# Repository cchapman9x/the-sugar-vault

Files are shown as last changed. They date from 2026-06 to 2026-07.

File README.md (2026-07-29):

# The Sugar Vault

<p align="center">
  Final build front view
  Final build front view
  Final build side view
</p>

<hr>

**Project Status:** Completed ✅

<hr>

## Project Overview

The Sugar Vault is an Arduino-controlled candy dispenser that uses an Arduino Nano, NEMA 17 stepper motor, A4988 stepper motor driver, push button, LED indicator, DC-DC buck converter, and 3D-printed mechanical parts to dispense candy.

The goal of this project was to design and build a functional candy dispensing machine that uses a motorized dispensing system instead of a traditional hand-turned mechanical mechanism. The final system is activated when the user presses the green button on the front of the machine. When pressed, the button sends a signal to the Arduino Nano, which then controls the A4988 stepper motor driver. The motor driver powers the NEMA 17 stepper motor, causing the dispensing wheel to rotate. During the dispensing cycle, the green LED turns on to indicate that the wheel is moving. One button press rotates the dispensing wheel 360° to release candy.

This project was built to refresh and strengthen my basic engineering skills while giving me a better understanding of how to format, document, and organize future electronics and mechanical design projects.

<hr>

## Main Components

<table>
  <tr>
    <th>Component</th>
    <th>Image</th>
  </tr>

  <tr>
    <td>Arduino Nano</td>
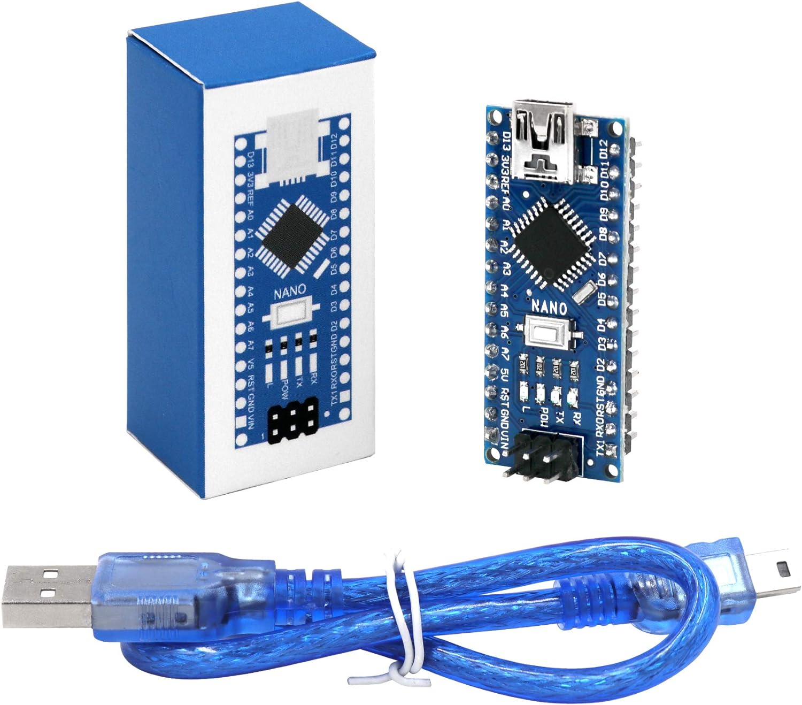
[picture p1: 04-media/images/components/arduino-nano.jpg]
Arduino Nano
    <td></td>
  </tr>

  <tr>
    <td>A4988 stepper motor driver</td>
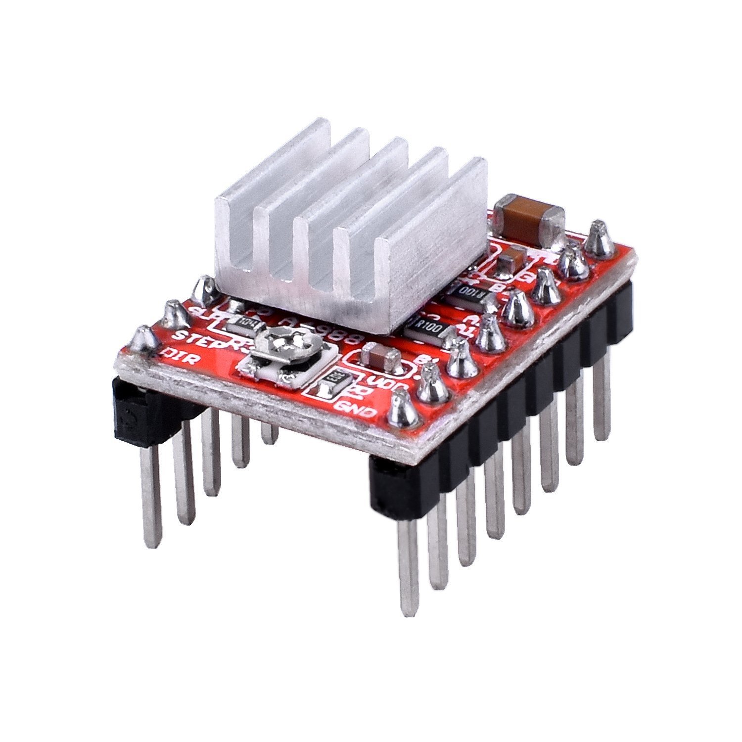
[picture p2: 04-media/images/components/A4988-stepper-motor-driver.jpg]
A4988 stepper motor driver
    <td></td>
  </tr>

  <tr>
    <td>NEMA 17 stepper motor</td>
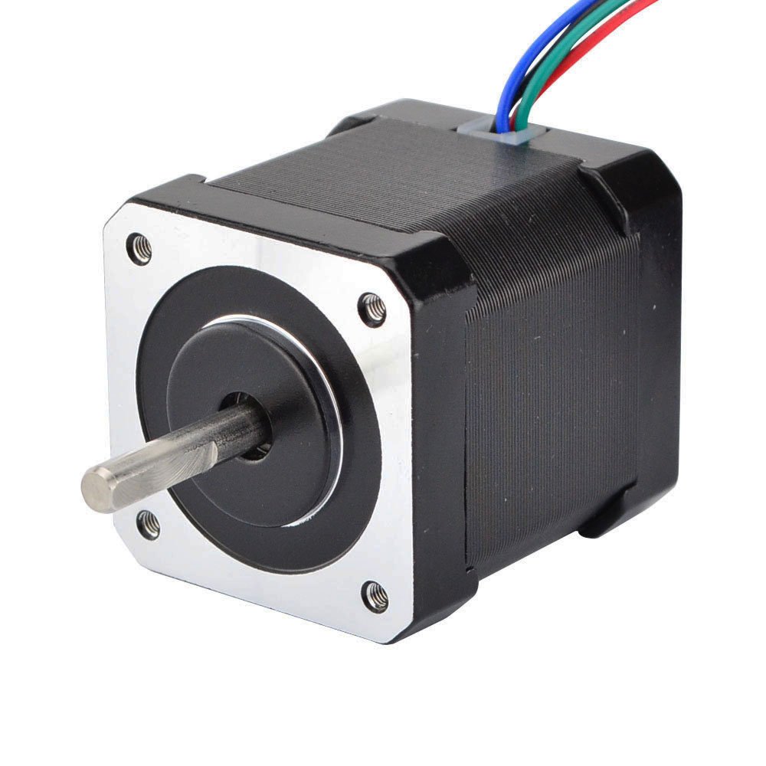
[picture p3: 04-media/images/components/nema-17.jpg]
NEMA 17 stepper motor
    <td></td>
  </tr>

  <tr>
    <td>12V 2A power supply</td>
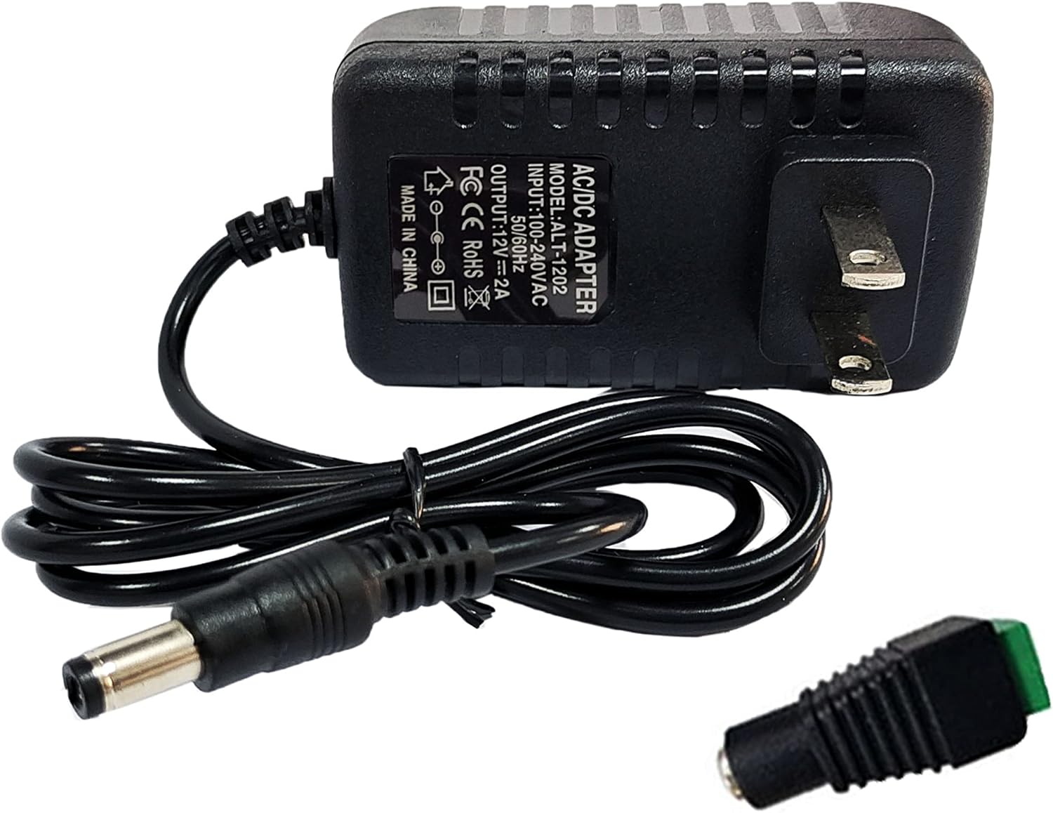
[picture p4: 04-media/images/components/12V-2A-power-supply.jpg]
12V 2A power supply
    <td></td>
  </tr>

  <tr>
    <td>DC-DC buck converter</td>
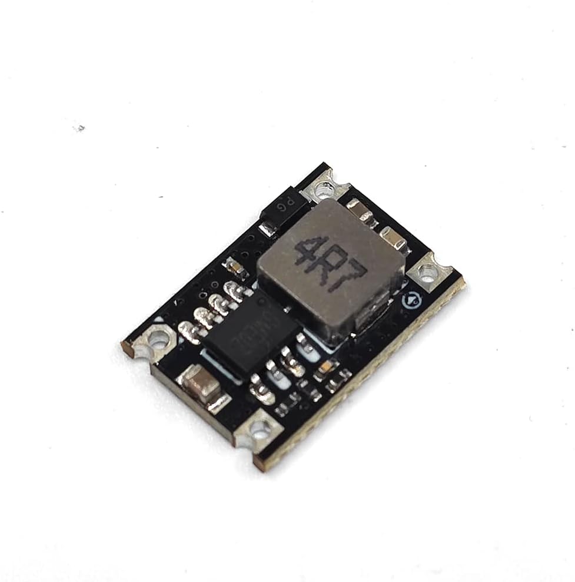
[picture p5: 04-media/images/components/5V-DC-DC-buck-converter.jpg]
DC-DC buck converter
    <td></td>
  </tr>

  <tr>
    <td>Push button</td>
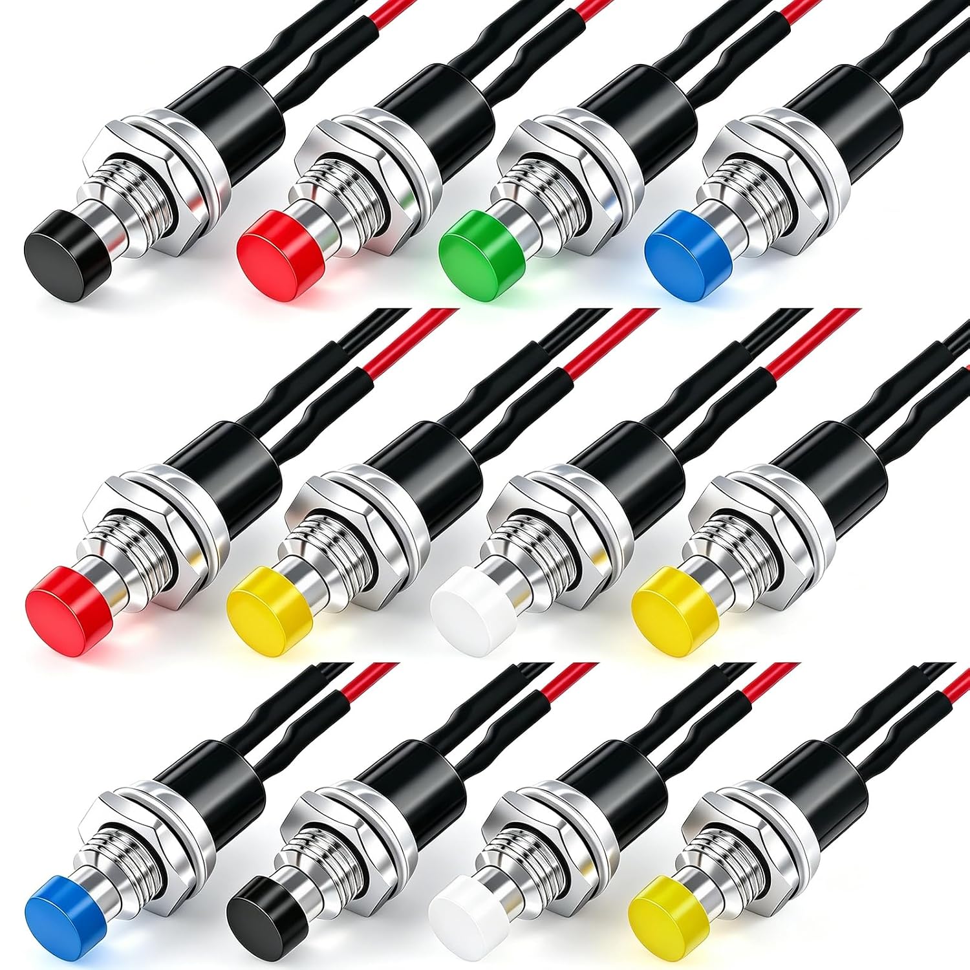
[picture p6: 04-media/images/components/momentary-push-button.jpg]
Push button
    <td></td>
  </tr>

  <tr>
    <td>Green LED</td>
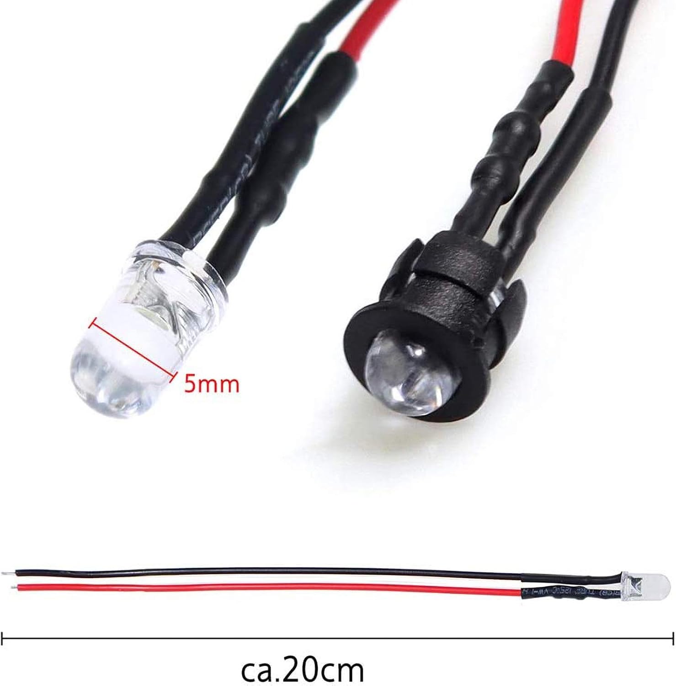
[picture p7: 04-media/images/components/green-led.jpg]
Green LED
    <td></td>
  </tr>

  <tr>
    <td>2.2 kΩ resistor</td>
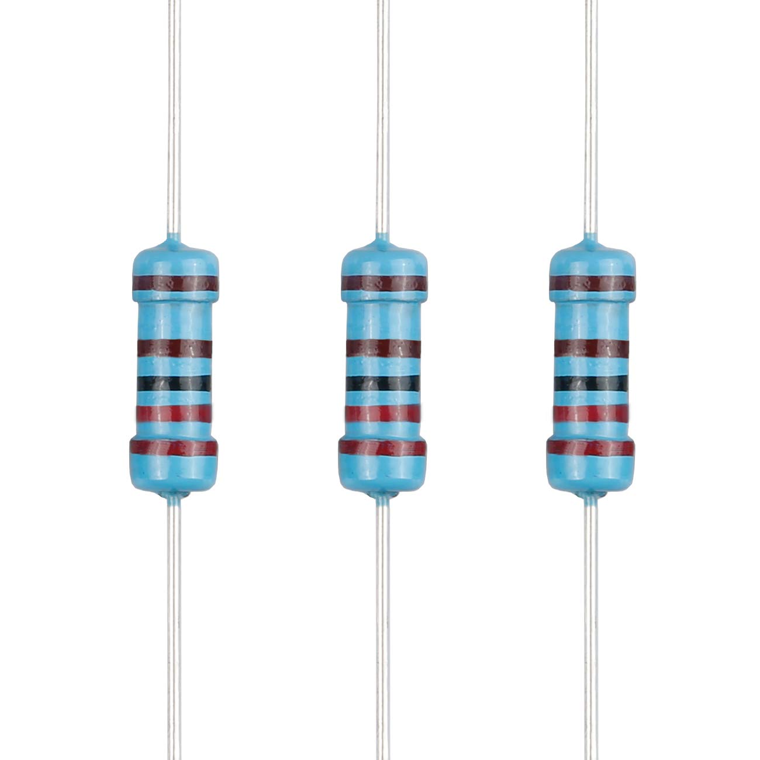
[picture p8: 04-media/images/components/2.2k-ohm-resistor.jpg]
2.2 kΩ resistor
    <td></td>
  </tr>

  <tr>
    <td>220 µF 25V electrolytic capacitor</td>
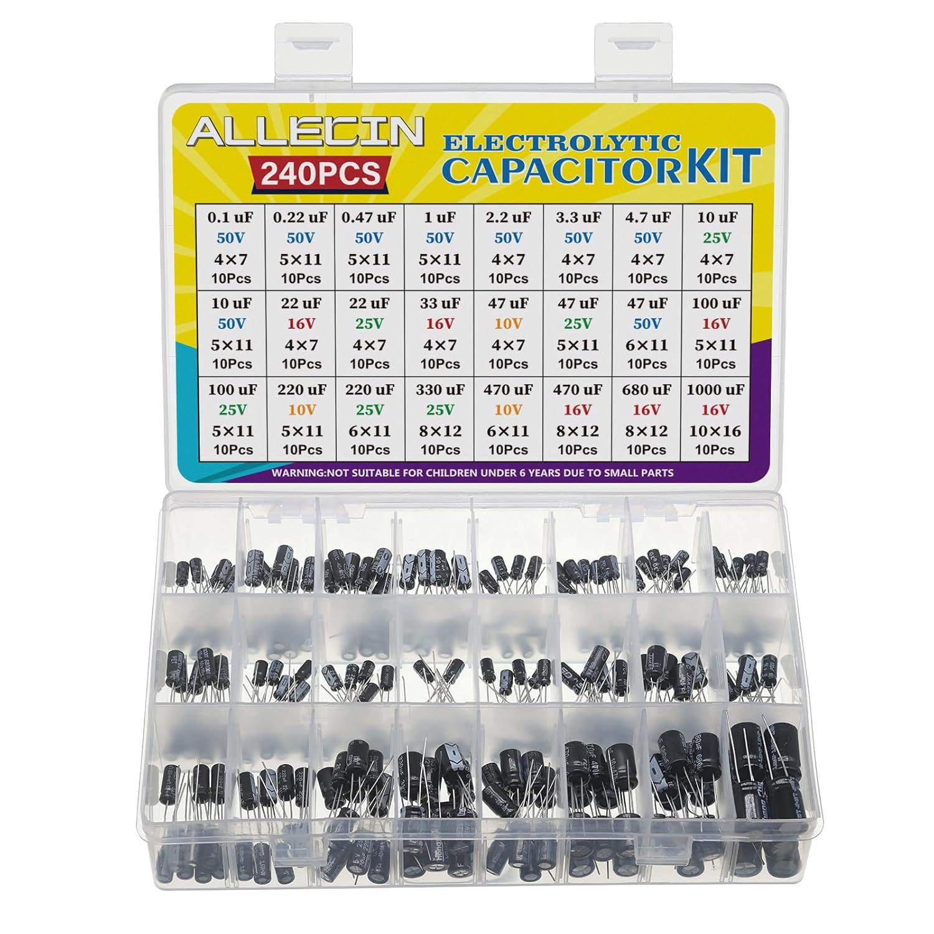
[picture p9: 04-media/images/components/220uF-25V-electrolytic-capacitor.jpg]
220 µF 25V electrolytic capacitor
    <td></td>
  </tr>

  <tr>
    <td>Red & White PETG</td>
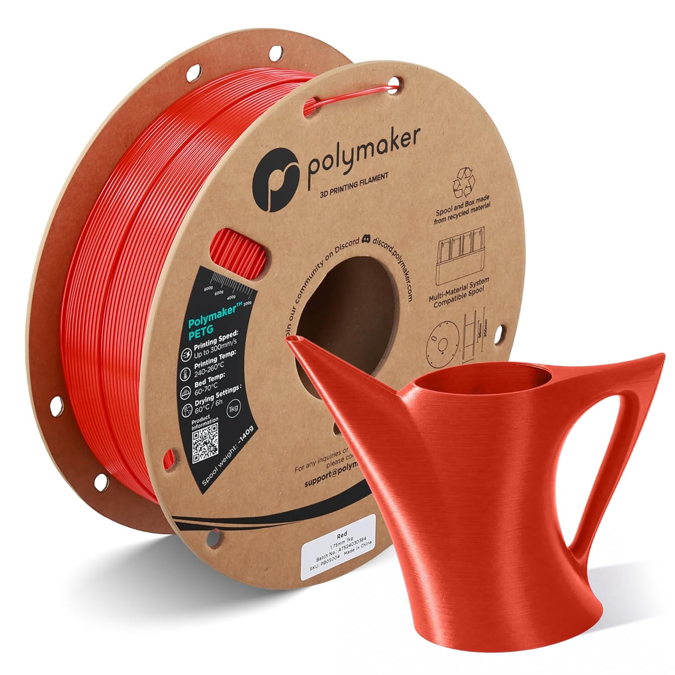
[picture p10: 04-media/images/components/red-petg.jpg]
    <td></td>
  </tr>

  <tr>
    <td>12" Clear Acrylic Tube</td>
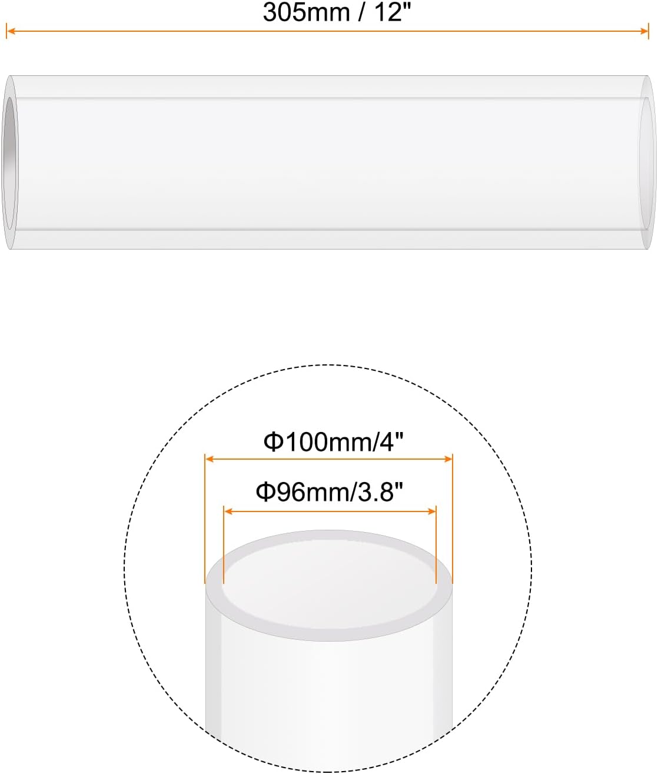
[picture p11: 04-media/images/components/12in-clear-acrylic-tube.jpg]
    <td></td>
  </tr>
</table>

<hr>

## Full Project Documentation

📄 [Open the complete Sugar Vault technical report](01-docs/the-sugar-vault-main.pdf)

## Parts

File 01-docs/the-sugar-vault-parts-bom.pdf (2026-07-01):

# The Sugar Vault

An Arduino controlled candy & chocolate dispensing machine

PARTS+BOM

Start Date: 5/18/2026
End Date: 6/28/2026
Software Used: Google Docs, SOLIDWORKS, draw.io, Arduino IDE, GitHub, Bambu Studio Project GitHub: https://github.com/cchapman9x/the-sugar-vault

Project Creator:
- Caleb Chapman | Montgomery College | Electrical Engineering

Parts Required

Part | Qty | Purpose
Arduino Nano | x1 | Main microcontroller used to control the dispenser
A4988 Stepper Motor Driver | x1 | Controls the NEMA 17 stepper motor
NEMA 17 Stepper Motor | x1 | Rotates the dispensing wheel
12V 2A Power Supply | x1 | Main external power source for the system
DC-DC Buck Converter | x1 | Steps the 12V supply down to a safe voltage for the Arduino
Momentary Push Button | x1 | User input used to start the dispensing cycle
Green LED | x1 | Visual indicator that turns on while dispensing
2.2kΩ Resistor | x1 | Limits current for the LED
220μF 25V Electrolytic Capacitor | x1 | Helps smooth power near the stepper motor driver
Red & White Filament | As Needed | Used to create the 3D printed parts
12” Clear Acrylic Tube ⌀100mm / 4” | x1 | Used to store the candy and acts as the hopper of the system

1

Jumper Wires / Hookup Wires | As Needed | Used to connect the circuit components
Screw Terminals / Connectors | As Needed | Used for power and wiring connections
Breadboard-Style Perfboard / Prototyping Board | x2 | Used to mount and organize the circuit components in a more permanent layout than a standard breadboard
M3x8mm Threaded Heat-Set Inserts | x16 | Used for assembling the machine together
M3x10mm Screws | x20 | Used for assembling the machine and motor

Tools Required

Tool | Purpose
3D Printer | Printed the mechanical enclosure and dispensing parts
Wire Strippers | Removed insulation from wires
Wire Cutters | Cut wires to the correct length
Pliers | Used to remove support material and grip small parts/wires during assembly
Small Screwdriver Set | Tightened terminals, screws, and electronics connections
Soldering Iron | Used for permanent or semi-permanent electrical connections
Solder | Used with the soldering iron to connect wires/components
Multimeter | Checked voltage, continuity, and wiring connections
Heat Shrink | Used to insulate and protect soldered wire connections
Calipers | Used for part measuring

2

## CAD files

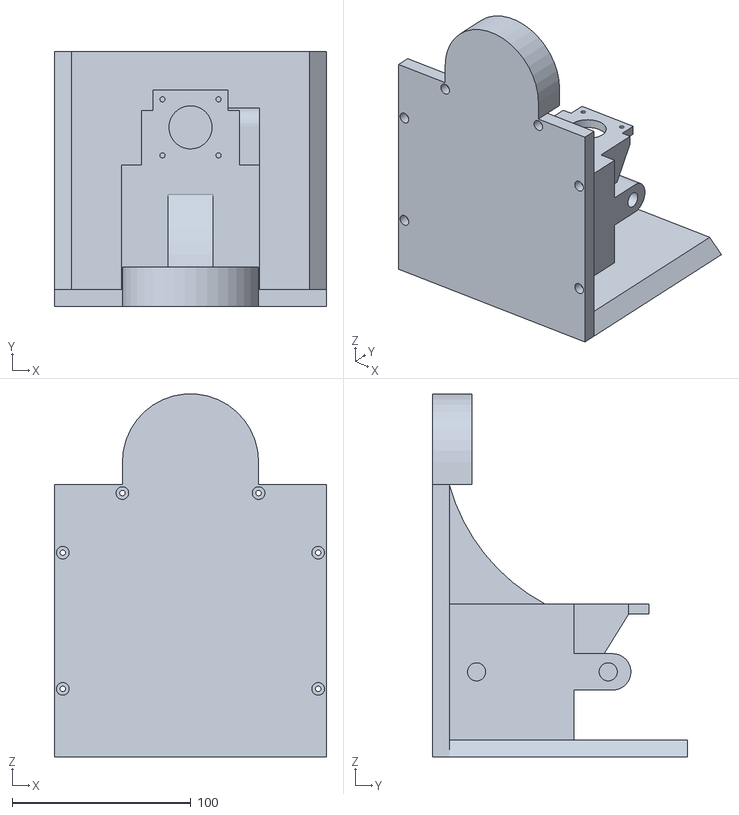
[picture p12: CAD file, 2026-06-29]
02-engineering-design/cad-files/3d-stl-files/sugar-vault-main-base.STL
152.4 x 142.9 x 203.1

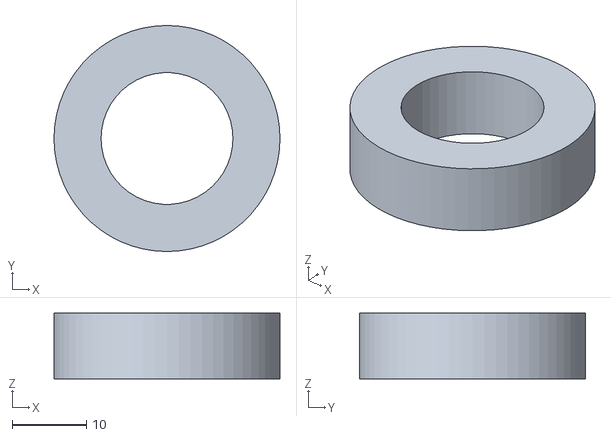
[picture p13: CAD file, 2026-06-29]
02-engineering-design/cad-files/3d-stl-files/sugar-vault-led-ring.STL
30.5 x 30.5 x 8.89

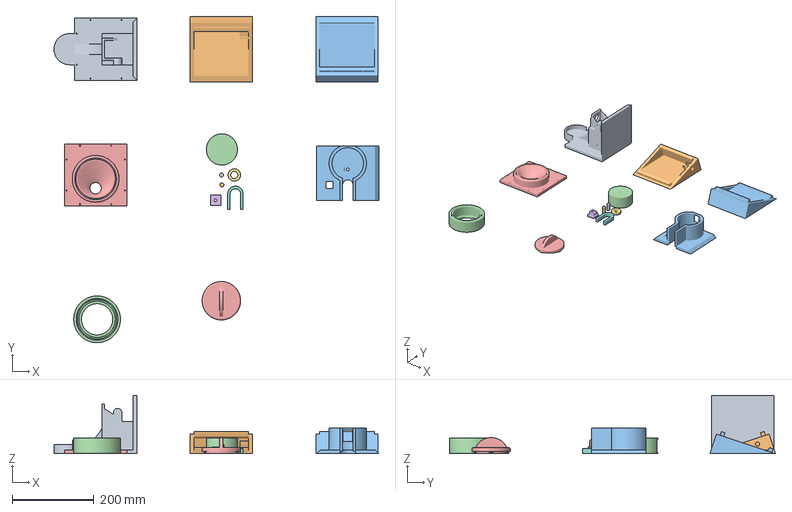
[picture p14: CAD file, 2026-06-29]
02-engineering-design/cad-files/3d-stl-files/sugar-vault-stl-package.3mf
793.8 x 797.2 x 142.9 mm
SV_base.STL
SV_right.STL
SV_left.STL
SV_wheel.STL
SV_top.STL
SV_buttonholder.STL
SV_ledring.STL
SV_doorway.STL
SV_circuitBoardStandOffs.STL x 2
SV_front.STL
SV_lid_part1.STL
SV_lid_part2.STL

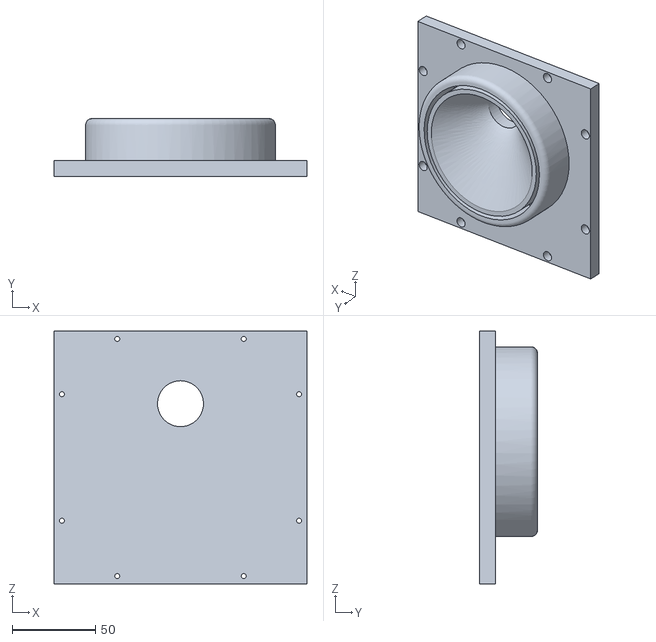
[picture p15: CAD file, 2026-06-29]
02-engineering-design/cad-files/3d-stl-files/sugar-vault-top-hopper-holder.STL
152.4 x 34.9 x 152.4

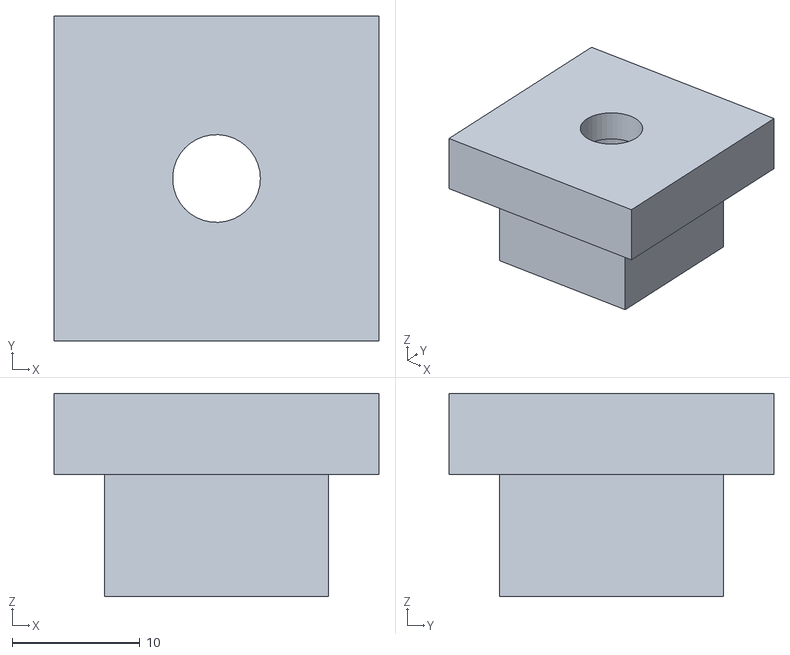
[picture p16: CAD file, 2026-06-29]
02-engineering-design/cad-files/3d-stl-files/sugar-vault-button-holder.STL
25.4 x 25.4 x 15.9

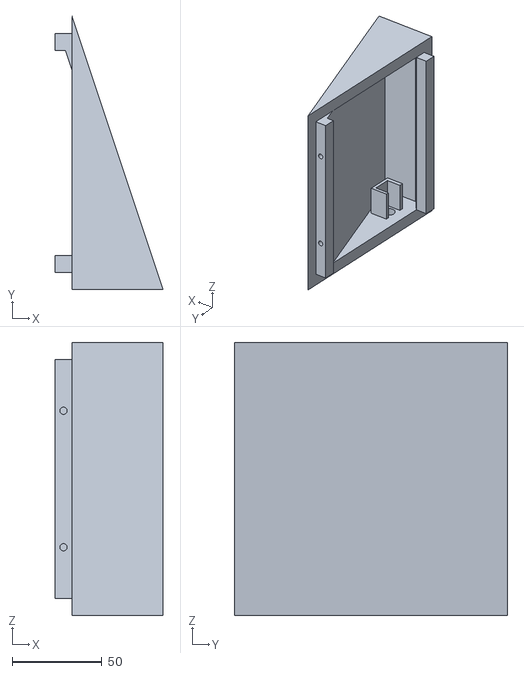
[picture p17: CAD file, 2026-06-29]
02-engineering-design/cad-files/3d-stl-files/sugar-vault-right-wall.STL
60.3 x 152.4 x 152.4

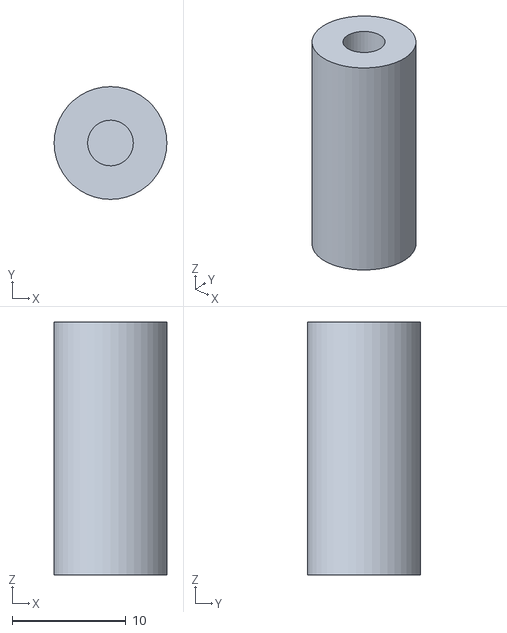
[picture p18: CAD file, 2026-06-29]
02-engineering-design/cad-files/3d-stl-files/sugar-vault-circuit-board-standoffs.STL
9.91 x 9.91 x 22.2

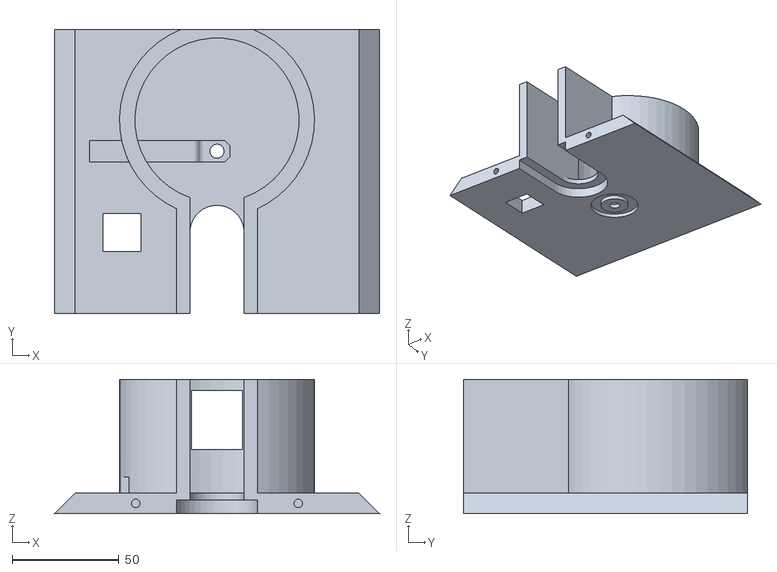
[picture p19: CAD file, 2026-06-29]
02-engineering-design/cad-files/3d-stl-files/sugar-vault-front-wall.STL
152.4 x 133.4 x 62.9

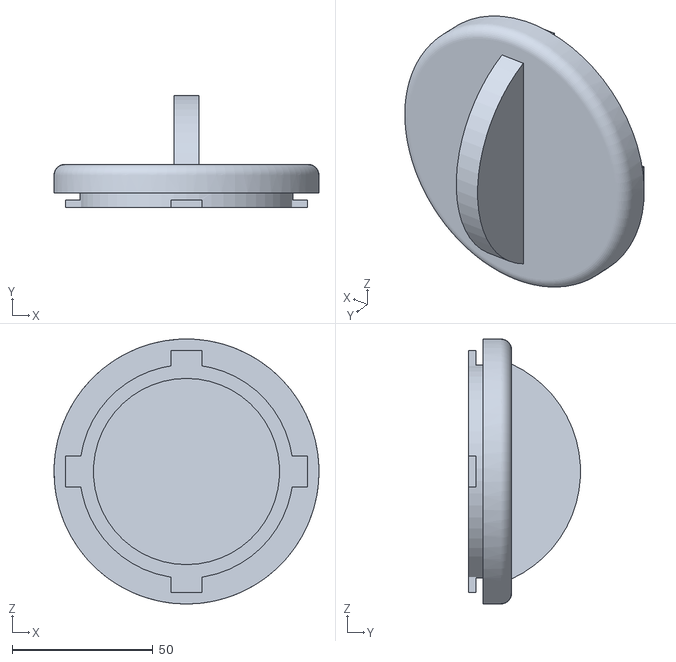
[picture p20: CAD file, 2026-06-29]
02-engineering-design/cad-files/3d-stl-files/sugar-vault-lid-part2.STL
94.0 x 39.6 x 94.0

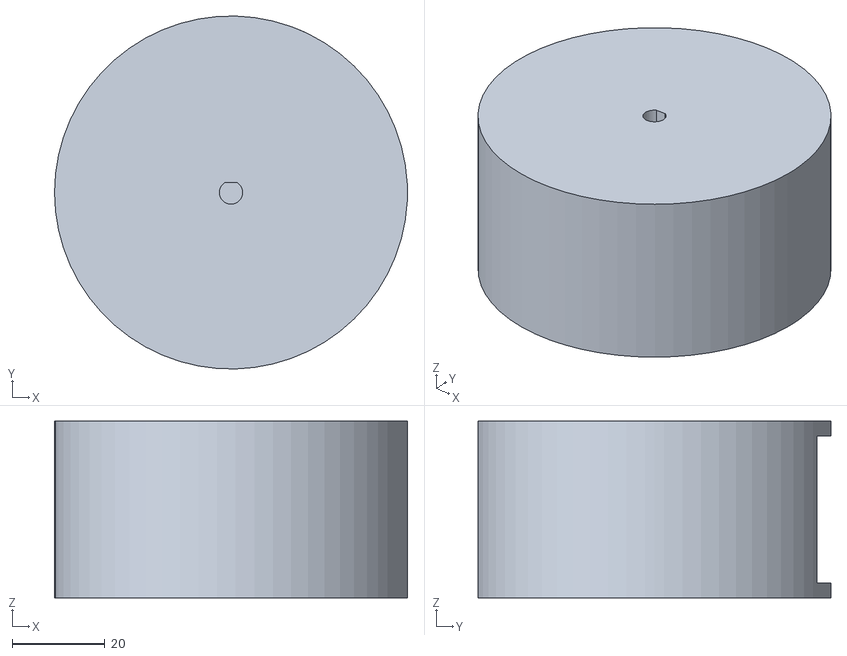
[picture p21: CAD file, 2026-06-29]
02-engineering-design/cad-files/3d-stl-files/sugar-vault-dispensing-wheel.STL
76.2 x 76.2 x 38.1

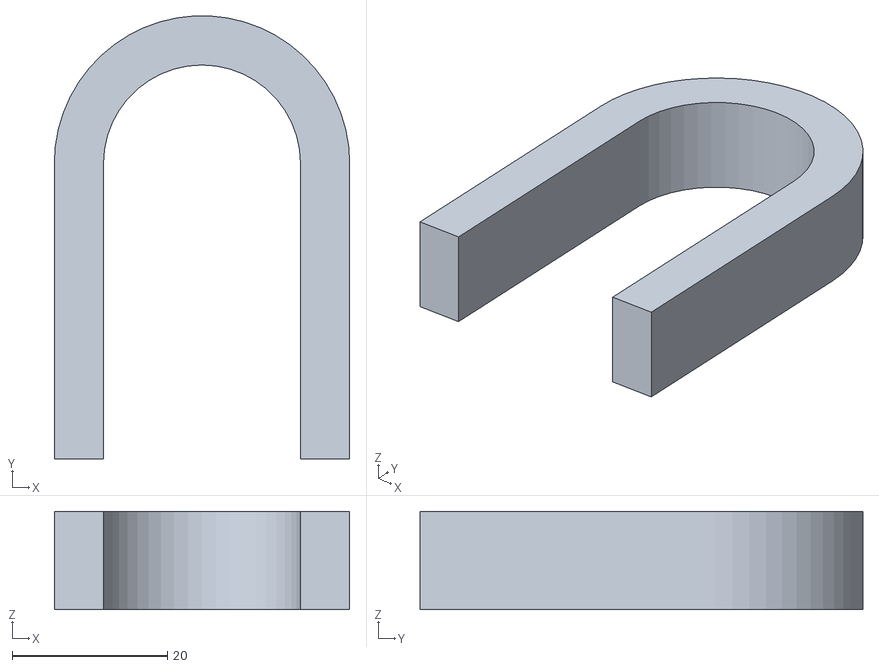
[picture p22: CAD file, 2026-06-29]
02-engineering-design/cad-files/3d-stl-files/sugar-vault-doorway-arch.STL
38.1 x 57.1 x 12.7

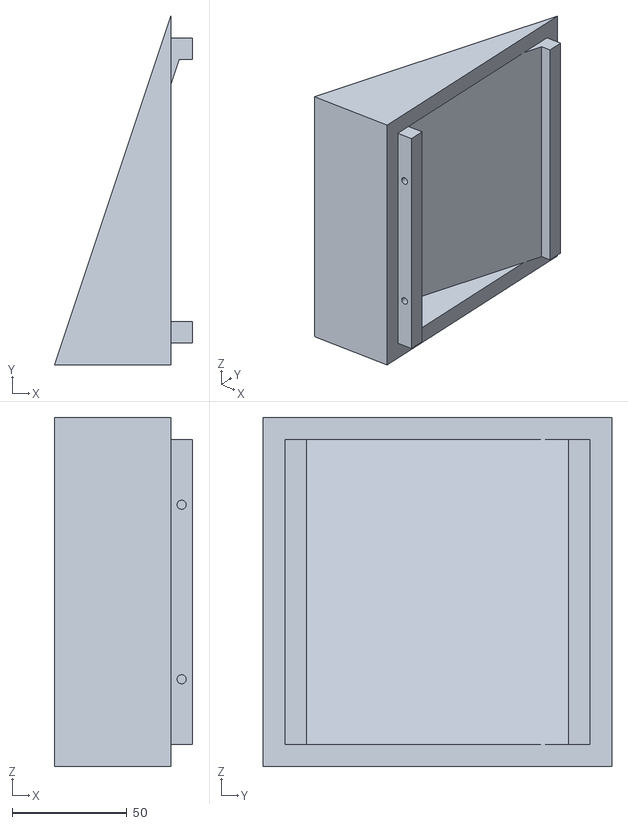
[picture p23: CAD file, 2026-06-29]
02-engineering-design/cad-files/3d-stl-files/sugar-vault-left-wall.STL
60.3 x 152.4 x 152.4

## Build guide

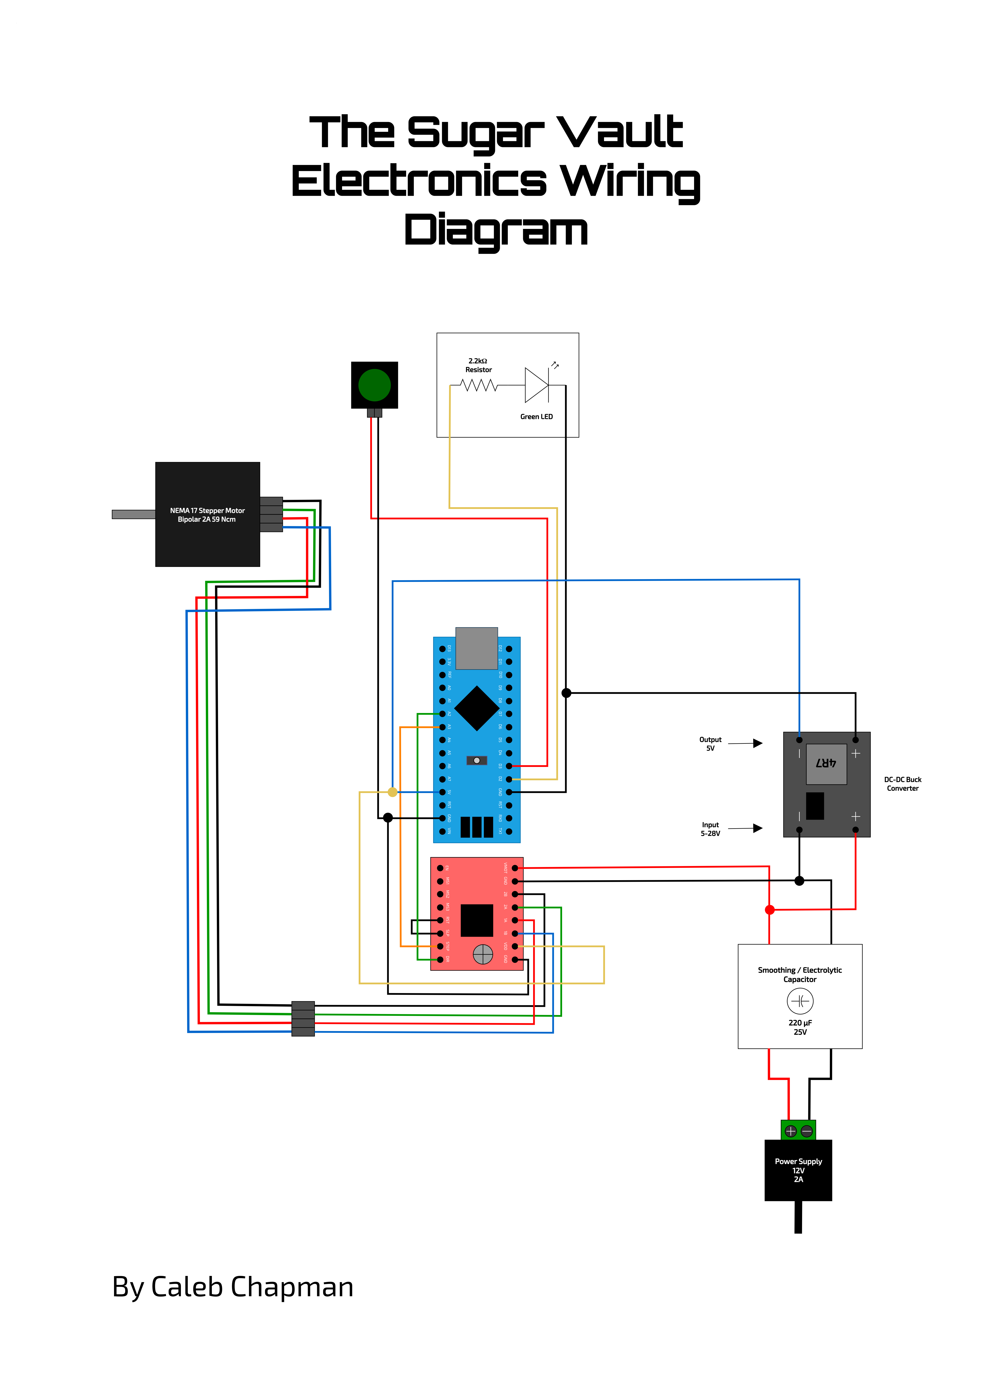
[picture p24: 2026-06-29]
02-engineering-design/electronics-wiring-diagram/sugar_vault_wiring_diagram.png

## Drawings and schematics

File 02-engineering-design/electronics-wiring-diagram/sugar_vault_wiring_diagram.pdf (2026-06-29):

# The Sugar Vault

# Electronics Wiring

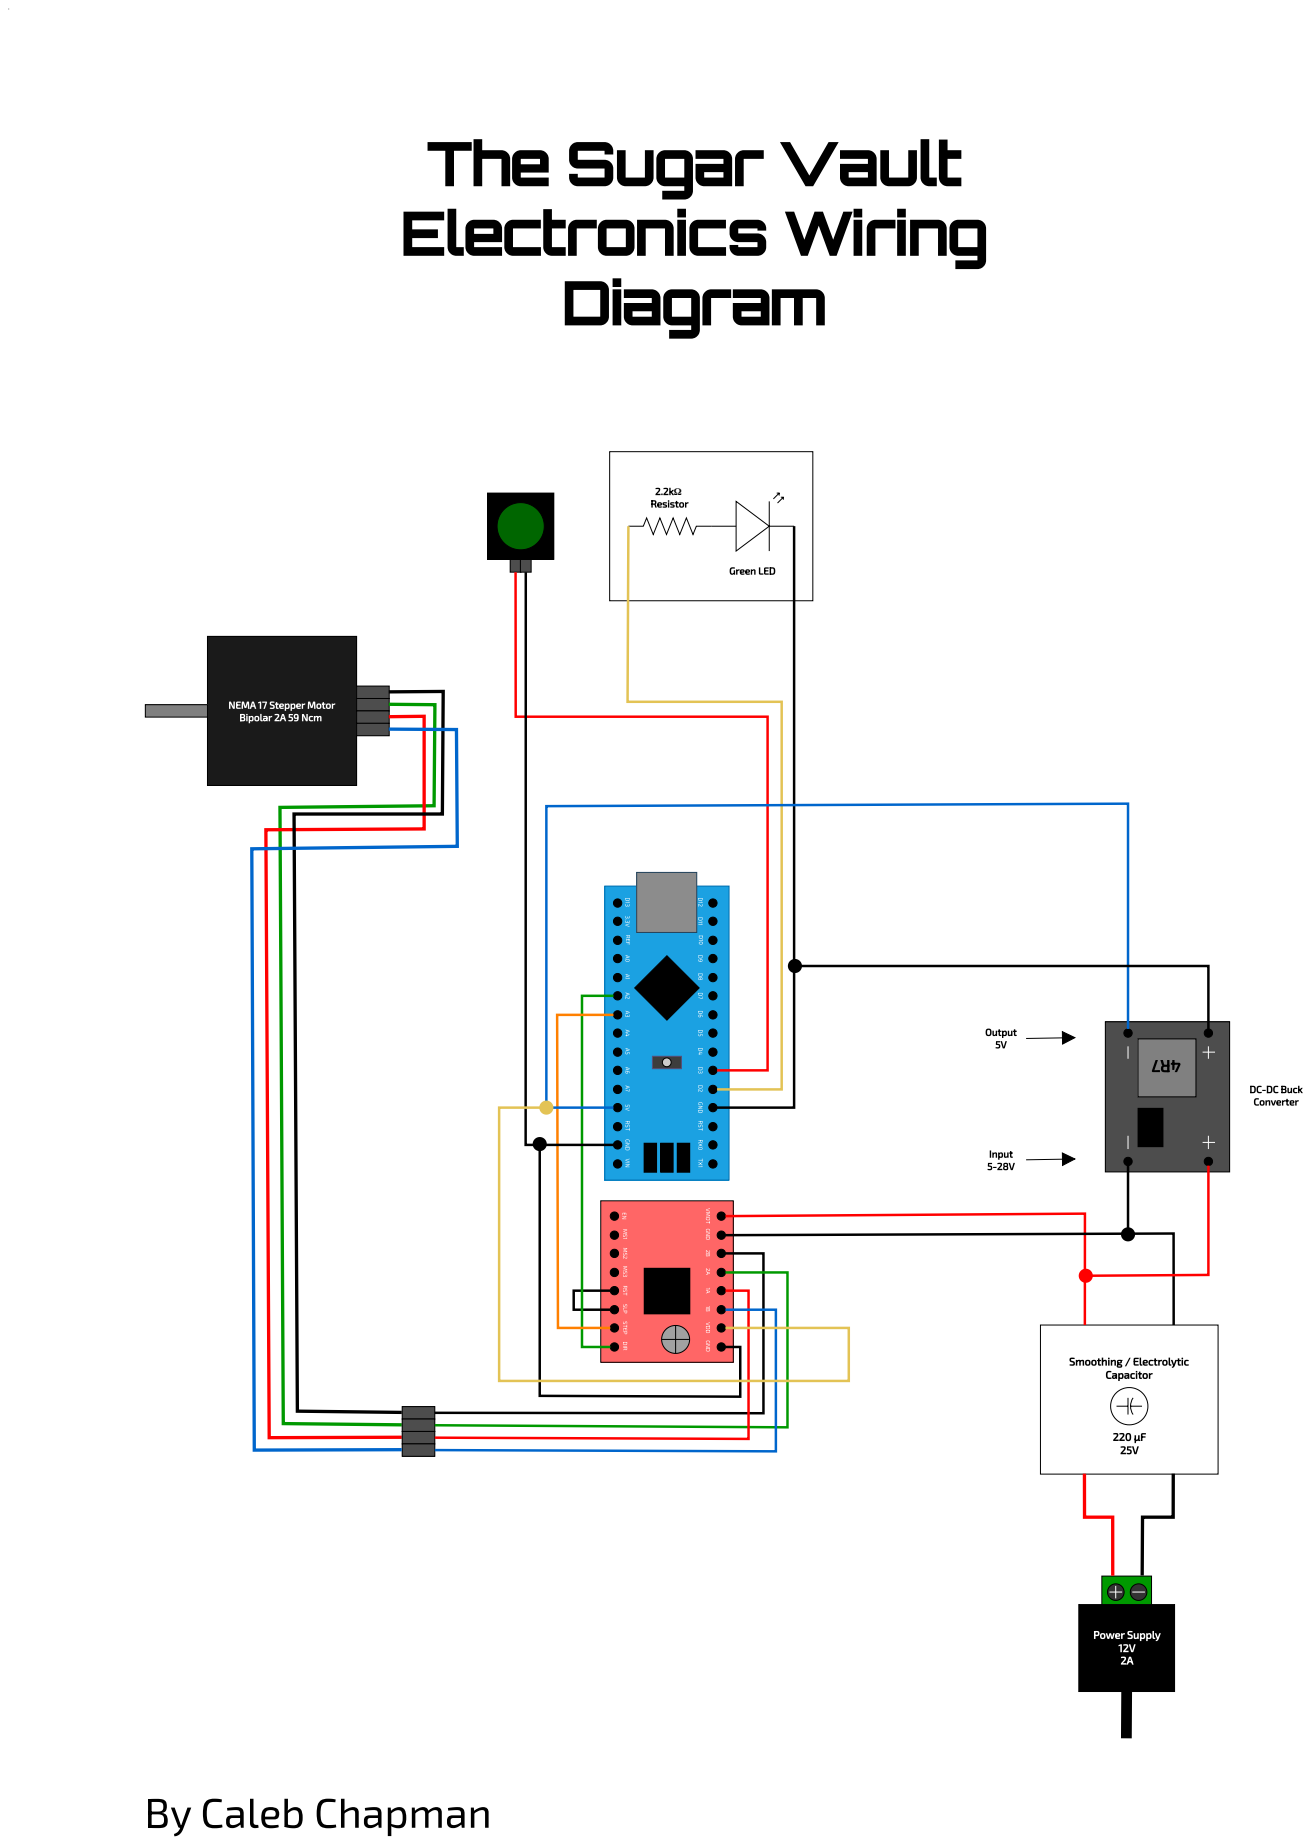
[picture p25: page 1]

D13 3.3V REF A0 A1 A2 A3 A4 A5 A6 A7 5V RST GND VIN

EN MS1 MS2 MS3 RST SLP STEP DIR

VMOT GND 2B 2A 1A 1B VDD GND

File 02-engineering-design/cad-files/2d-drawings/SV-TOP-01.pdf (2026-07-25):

.25

R.15

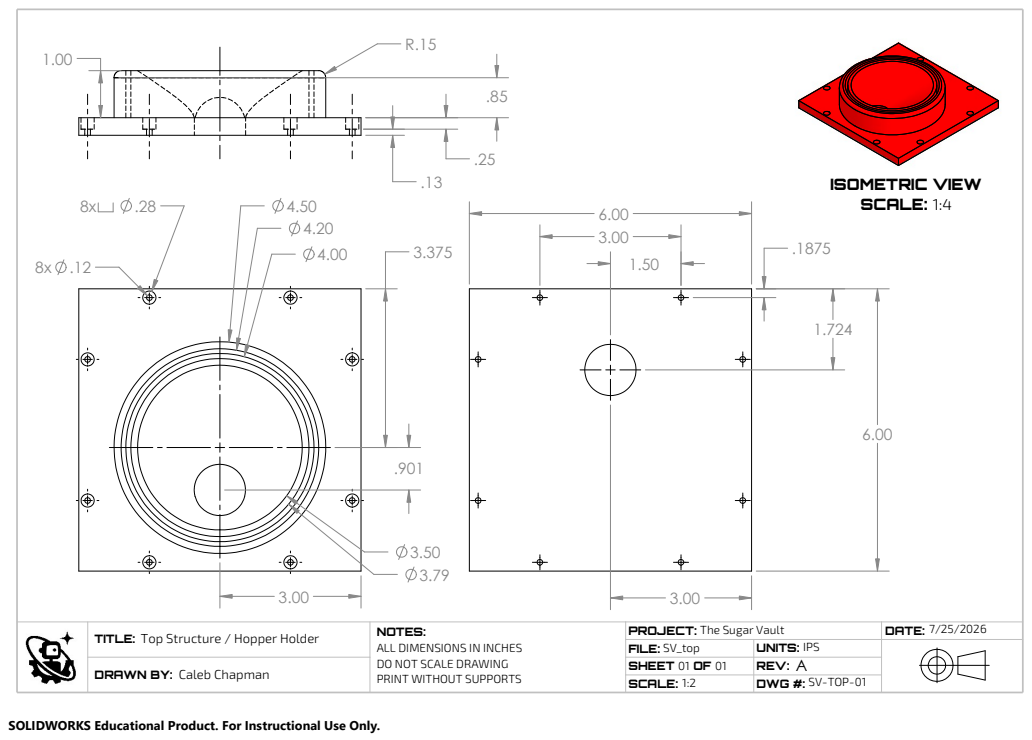
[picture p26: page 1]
ISOMETRIC VIEW; SCALE: 1:4

Top Structure / Hopper Holder TITLE: | NOTES: ALL DIMENSIONS IN INCHES DO NOT SCALE DRAWING PRINT WITHOUT SUPPORTS | The Sugar Vault PROJECT: | 7/25/2026 DATE :

FILE: SV_top | UNITS: IPS

DRAWN BY: Caleb Chapman | | SHEET 01 OF 01 | A REV: SV-TOP-01

SCALE: 1:2 | DWG # :

SOLIDWORKS Educational Product. For Instructional Use Only.

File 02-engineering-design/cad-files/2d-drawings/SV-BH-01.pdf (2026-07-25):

.42

.27

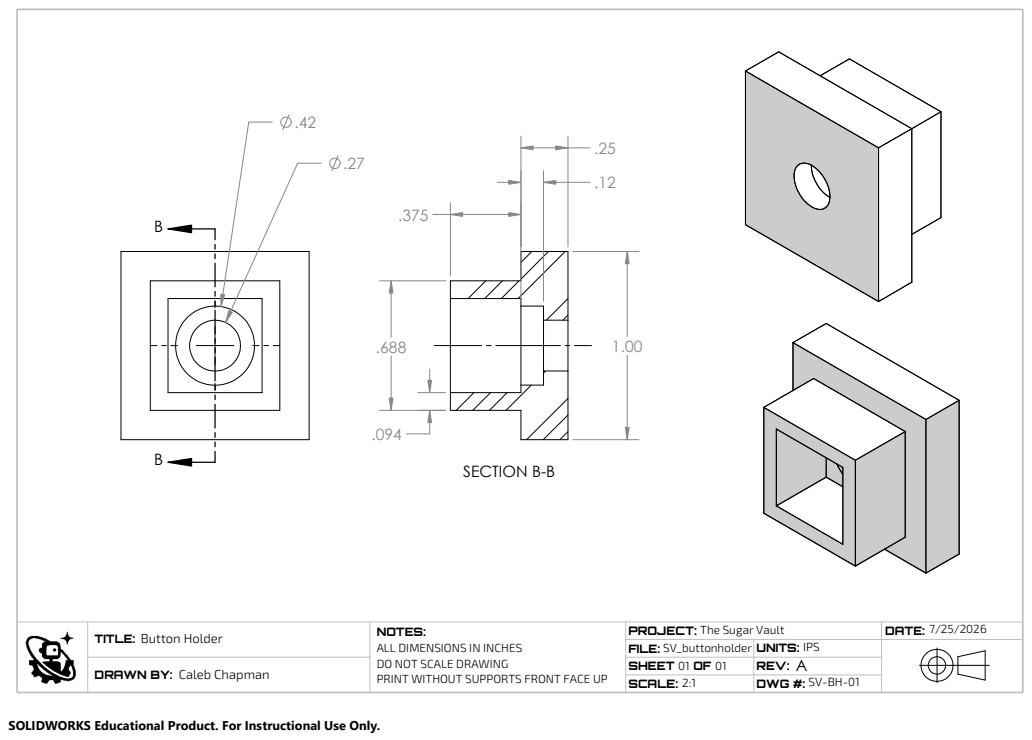
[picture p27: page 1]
SECTION B-B

Button Holder | NOTES: ALL DIMENSIONS IN INCHES DO NOT SCALE DRAWING PRINT WITHOUT SUPPORTS FRONT FACE UP | The Sugar Vault PROJECT: | 7/25/2026 DATE : TITLE:

FILE: SV_buttonholder | UNITS: IPS

DRAWN BY: | | SHEET 01 OF 01 | A REV :

SV-BH-01 Caleb Chapman

SCALE: 2:1 | DWG # :

SOLIDWORKS Educational Product. For Instructional Use Only.

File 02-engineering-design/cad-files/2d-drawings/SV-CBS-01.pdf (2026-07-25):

.158
.39

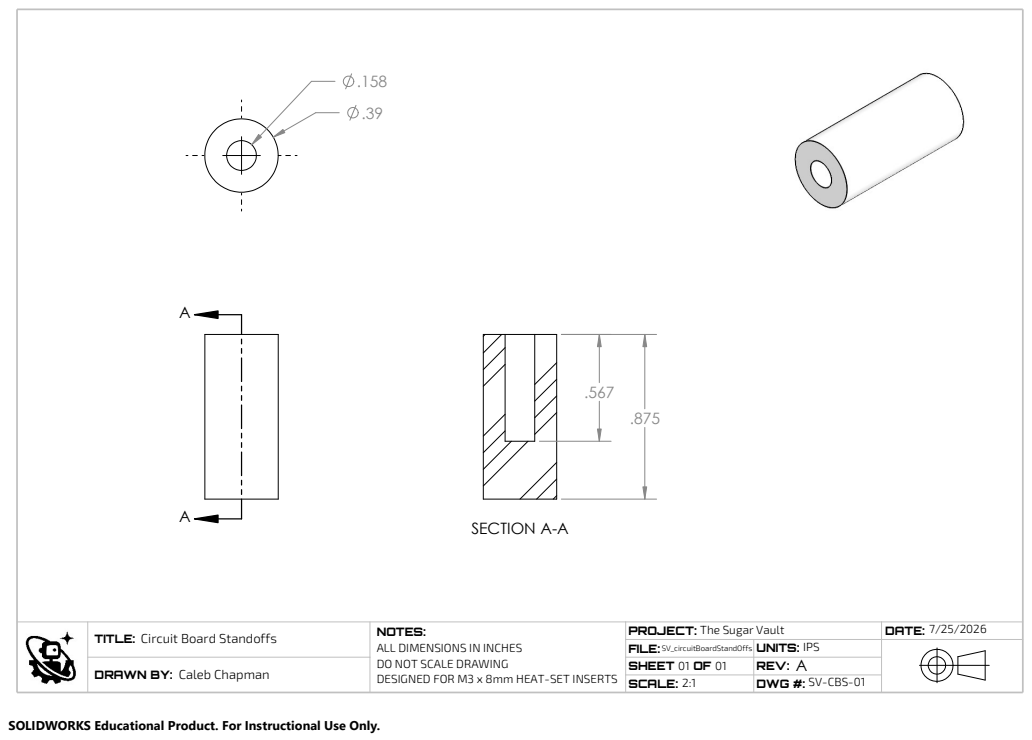
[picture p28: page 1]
SV-CBS-01 Caleb Chapman; SECTION A-A

Circuit Board Standoffs TITLE: | NOTES: ALL DIMENSIONS IN INCHES DO NOT SCALE DRAWING DESIGNED FOR M3 x 8mm HEAT-SET INSERTS | The Sugar Vault PROJECT: | : 7/25/2026 DATE

FILE: SV_circuitBoardStandOffs | UNITS: IPS

DRAWN BY: | | SHEET 01 OF 01 | A REV

2:1 SCALE: | DWG # :

SOLIDWORKS Educational Product. For Instructional Use Only.

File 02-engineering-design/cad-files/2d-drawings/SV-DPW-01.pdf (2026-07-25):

1.50

.10 | 1.25

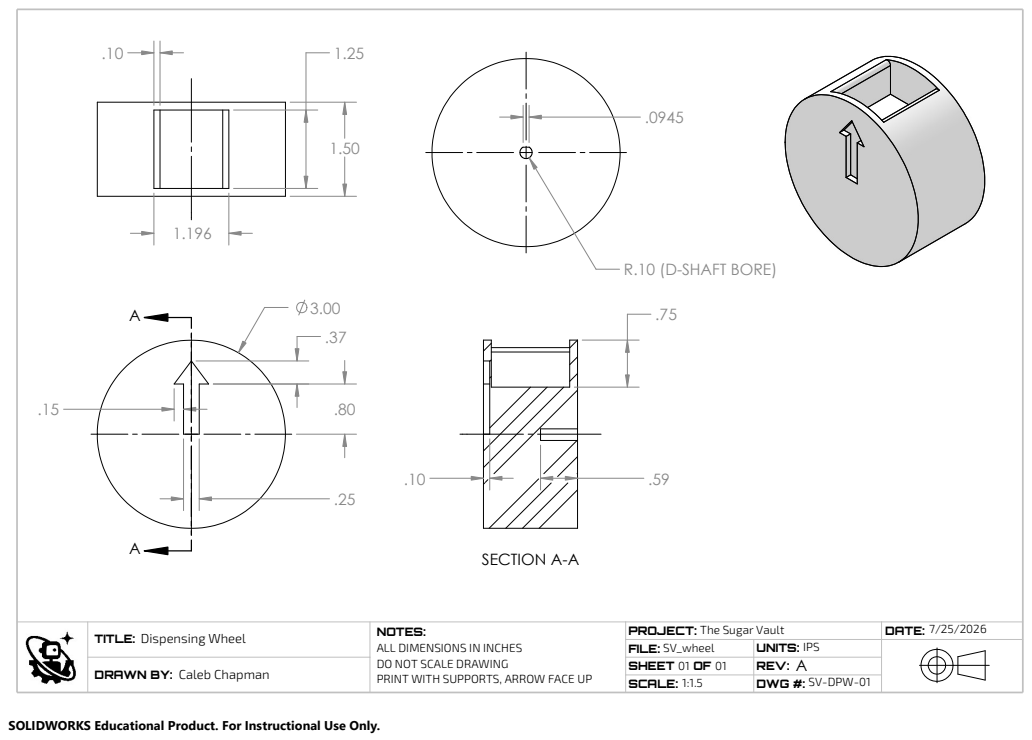
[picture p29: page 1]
SECTION A-A; R.10 (D-SHAFT BORE)

Dispensing Wheel TITLE: | NOTES: ALL DIMENSIONS IN INCHES DO NOT SCALE DRAWING PRINT WITH SUPPORTS, ARROW FACE UP | The Sugar Vault PROJECT: | 7/25/2026 DATE :
Caleb Chapman DRAWN BY: | | SHEET 01 OF 01 | A REV :

FILE: SV_wheel | UNITS: IPS

SCALE: 1:1.5 | DWG # : SV-DPW-01

SOLIDWORKS Educational Product. For Instructional Use Only.

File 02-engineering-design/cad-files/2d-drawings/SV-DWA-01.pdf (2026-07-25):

R.75 | R.50

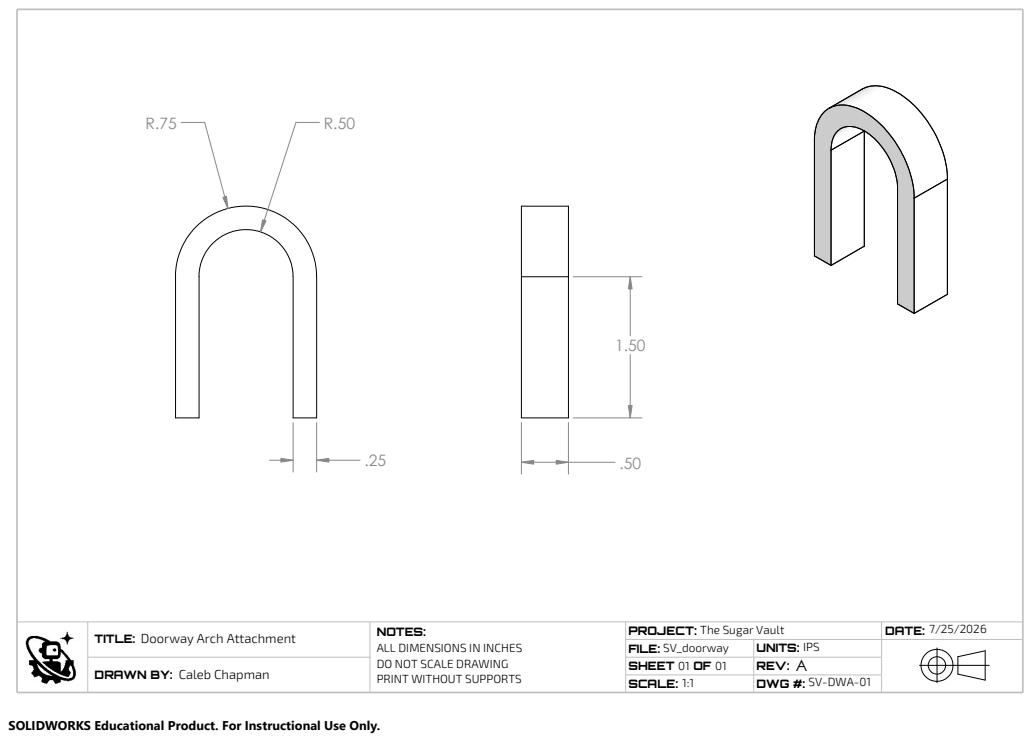
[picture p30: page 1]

Doorway Arch Attachment | NOTES: ALL DIMENSIONS IN INCHES DO NOT SCALE DRAWING PRINT WITHOUT SUPPORTS | The Sugar Vault PROJECT: | 7/25/2026 DATE : TITLE:

FILE: SV_doorway | UNITS: IPS

DRAWN BY: | | SHEET 01 OF 01 | A REV :

SV-DWA-01 Caleb Chapman

SCALE: 1:1 | DWG # :

SOLIDWORKS Educational Product. For Instructional Use Only.

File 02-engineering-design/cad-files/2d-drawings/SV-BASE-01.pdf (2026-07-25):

1.24

.25

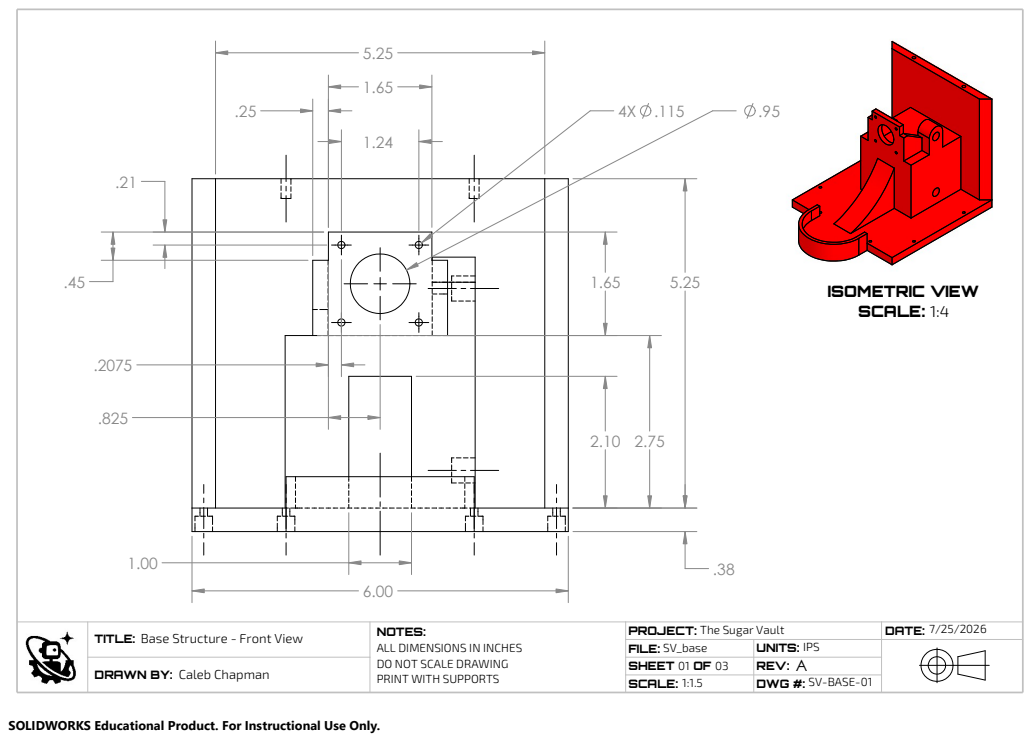
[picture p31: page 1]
ISOMETRIC VIEW SCALE: 1:4

Base Structure - Front View | NOTES: ALL DIMENSIONS IN INCHES DO NOT SCALE DRAWING PRINT WITH SUPPORTS | The Sugar Vault PROJECT: | 7/25/2026 DATE : TITLE:

FILE: SV_base | UNITS: IPS

DRAWN BY: | | SHEET 01 OF 03 | A REV :

SV-BASE-01 Caleb Chapman

SCALE: 1:1.5 | DWG # :

SOLIDWORKS Educational Product. For Instructional Use Only.

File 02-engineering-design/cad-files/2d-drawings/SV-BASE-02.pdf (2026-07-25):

R.40

2X .40

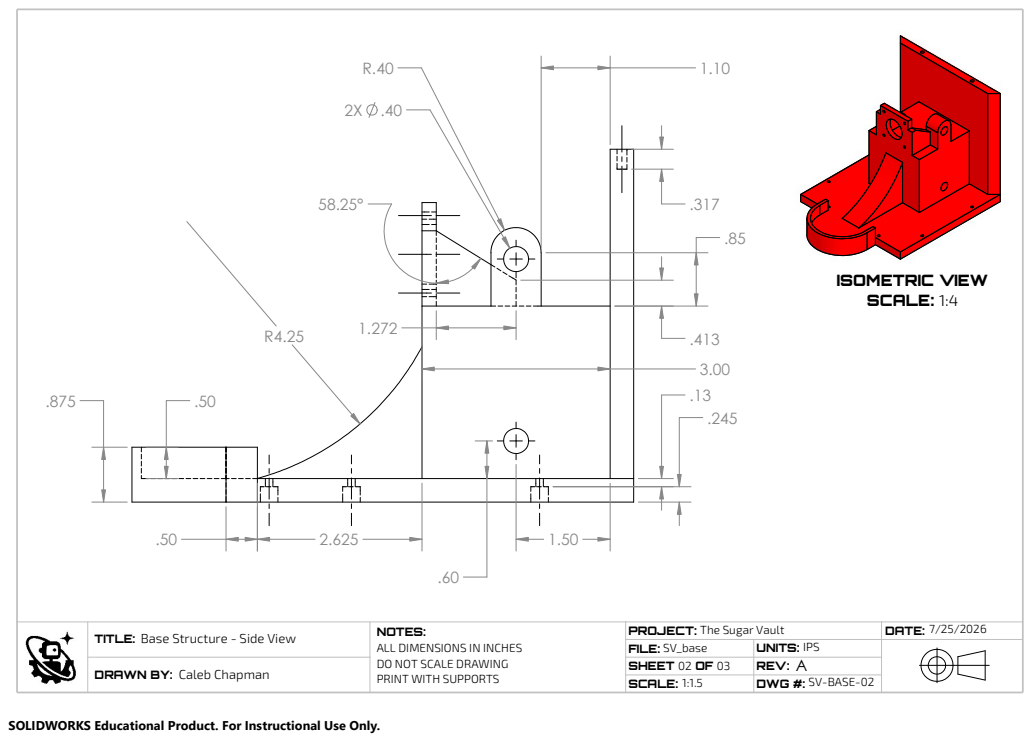
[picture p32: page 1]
ISOMETRIC VIEW SCALE: 1:4

Base Structure - Side View TITLE: | NOTES: ALL DIMENSIONS IN INCHES DO NOT SCALE DRAWING PRINT WITH SUPPORTS | The Sugar Vault PROJECT: | 7/25/2026 DATE :

FILE: SV_base | UNITS: IPS

Caleb Chapman DRAWN BY: | | SHEET 02 OF 03 | A REV :

SCALE: 1:1.5 | DWG # : SV-BASE-02

SOLIDWORKS Educational Product. For Instructional Use Only.

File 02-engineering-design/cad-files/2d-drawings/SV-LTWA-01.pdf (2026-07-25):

3.00

.1875

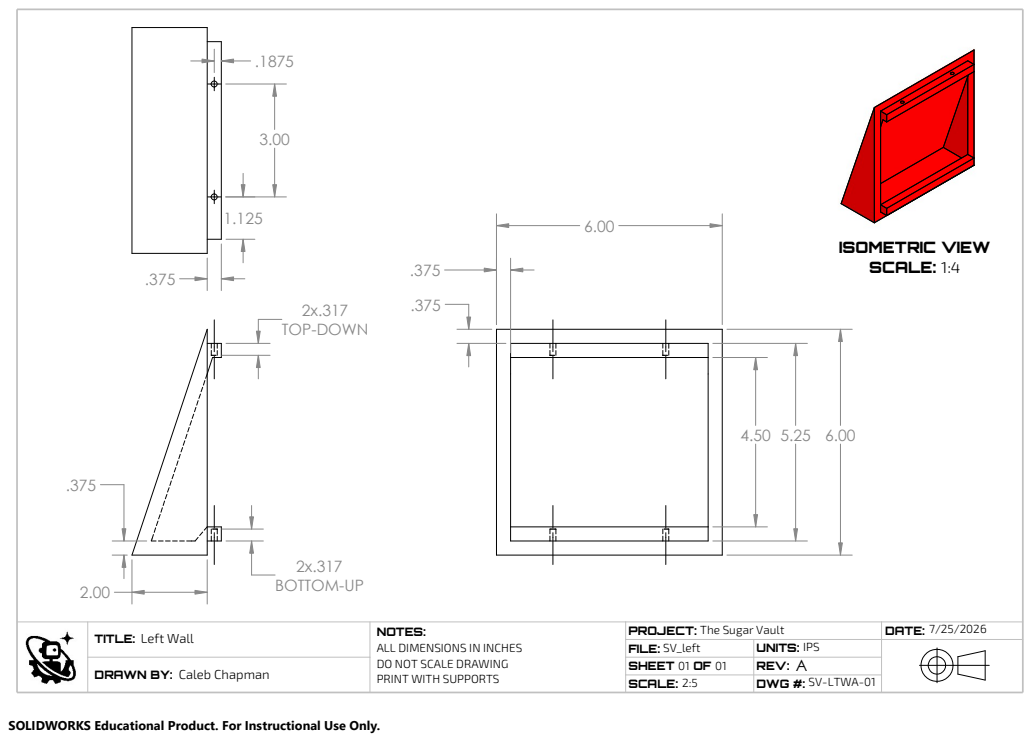
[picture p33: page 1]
ISOMETRIC VIEW SCALE: 1:4; 2x.317 BOTTOM-UP 2.00; TOP-DOWN

Left Wall | NOTES: ALL DIMENSIONS IN INCHES DO NOT SCALE DRAWING PRINT WITH SUPPORTS | The Sugar Vault PROJECT: SV_left TITLE: | 7/25/2026 DATE :

FILE: | UNITS: IPS

DRAWN BY: Caleb Chapman | | SHEET 01 OF 01 | A REV: SV-LTWA-01

2:5 SCALE: | DWG # :

SOLIDWORKS Educational Product. For Instructional Use Only.

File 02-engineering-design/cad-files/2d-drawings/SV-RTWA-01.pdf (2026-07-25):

.1875

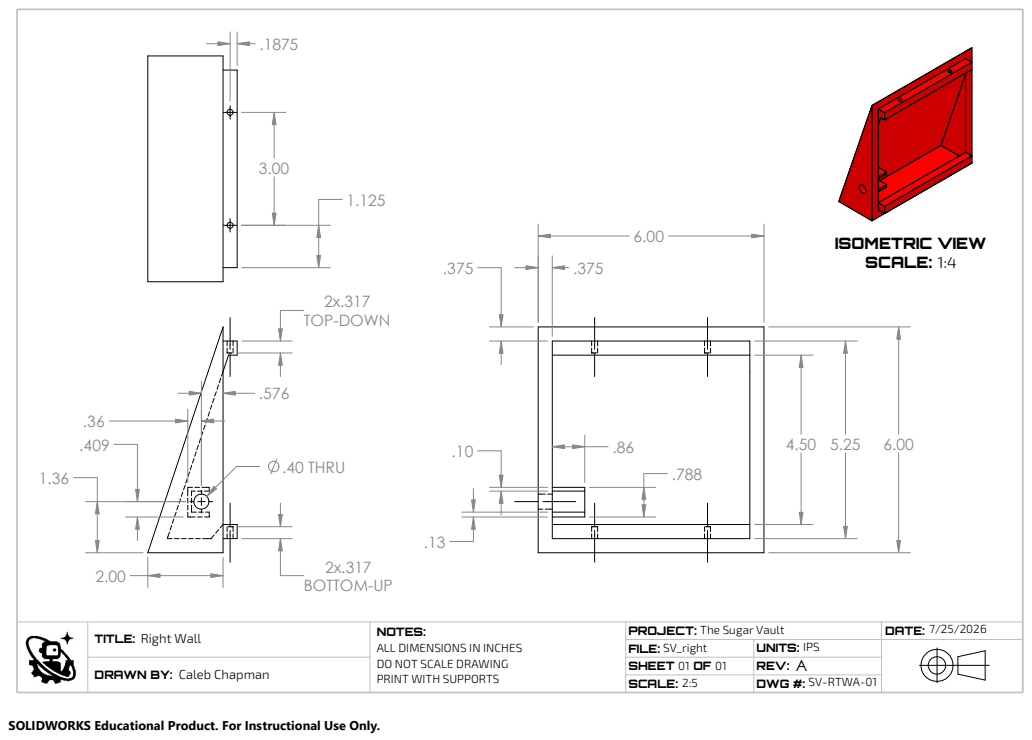
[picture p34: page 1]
2.00 BOTTOM-UP; TOP-DOWN; .40 THRU; ISOMETRIC VIEW SCALE: 1:4

Right Wall TITLE: | NOTES: ALL DIMENSIONS IN INCHES DO NOT SCALE DRAWING PRINT WITH SUPPORTS | The Sugar Vault PROJECT: | 7/25/2026 DATE :

FILE: SV_right | UNITS: IPS

DRAWN BY: Caleb Chapman | | SHEET 01 OF 01 | A REV: SV-RTWA-01

2:5 SCALE: | DWG # :

SOLIDWORKS Educational Product. For Instructional Use Only.

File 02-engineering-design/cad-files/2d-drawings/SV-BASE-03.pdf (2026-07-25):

## BOTTOM VIEW

## TOP VIEW

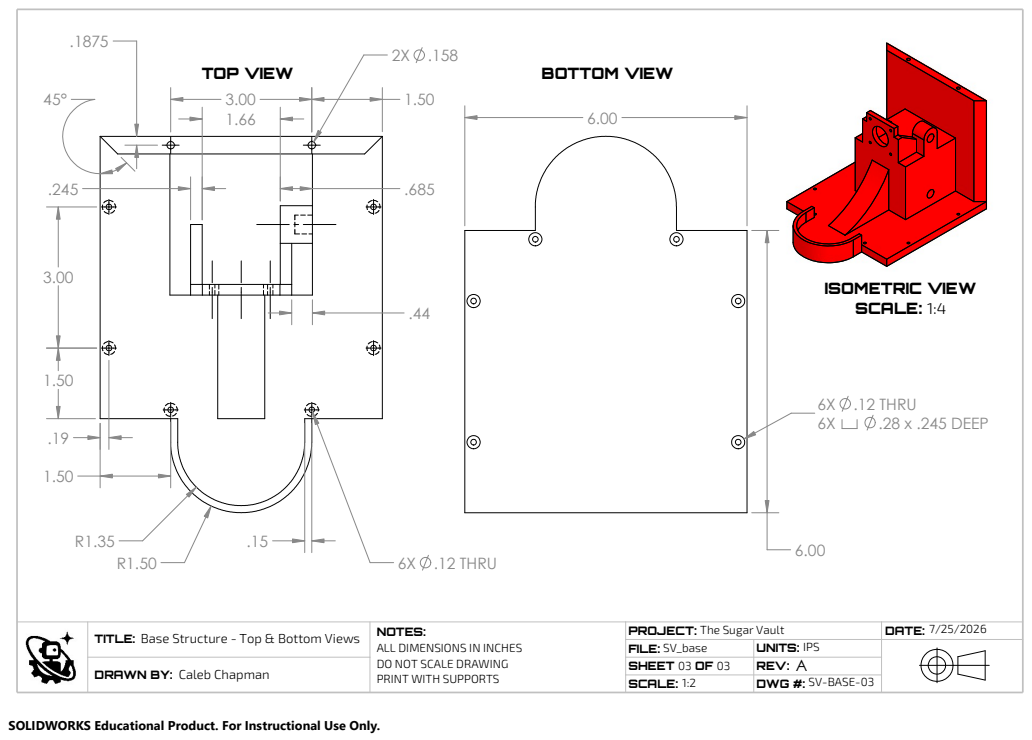
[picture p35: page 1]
ISOMETRIC VIEW SCALE:; 6X .12 THRU; .28 x .245 DEEP

Base Structure - Top & Bottom Views TITLE: | NOTES: ALL DIMENSIONS IN INCHES DO NOT SCALE DRAWING PRINT WITH SUPPORTS | The Sugar Vault PROJECT: | 7/25/2026 DATE :

FILE: SV_base | UNITS: IPS

DRAWN BY: | | SHEET 03 OF 03 | A REV :

SV-BASE-03 Caleb Chapman

SCALE: 1:2 | DWG # :

SOLIDWORKS Educational Product. For Instructional Use Only.

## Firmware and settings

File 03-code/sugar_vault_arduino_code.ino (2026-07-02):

// Please note that this code was made using a breadboard so the wire colors will be different than what's on the schematics

const int dirPin = A2; // Green wire
const int stePin = A3; // Orange wire
const int buttonPin = 3; // Blue wire
const int ledPin = 2; // Yellow wire

void setup() {
  // pinMode -> How we want the pins to behave, they behave as either an output or input
  // OUTPUT -> Pin that outputs information to something
  // INPUT -> Pin that recieves information from something

  pinMode(dirPin, OUTPUT); //A2 (Arduino pin) is outputting information to the direction pin on the motor driver
  pinMode(stePin, OUTPUT);

  pinMode(buttonPin, INPUT_PULLUP); //A4 inputs information to the arduino (turn on) -> INPUT_PULLUP stops button from floating and results in LOW when pin is pressed and HIGH when not pressed
  pinMode(ledPin, OUTPUT); //A5 tells the LED to turn on when the wheel is turning after the button is pressed

  // digitalWrite -> tells an OUTPUT pin to go either HIGH or LOW
  // HIGH for the dirPin on the driver means the motor goes CW
  // LOW for the dirPin on the driver means the motor goes CCW (We want CCW because of our design concept)
  digitalWrite(dirPin, LOW);
  digitalWrite(ledPin, HIGH); // Turns the LED ON
  digitalWrite(ledPin, LOW); // Turns the LED OFF

}

void loop() {
  bool dispenseCandy = digitalRead(buttonPin) == LOW; // LOW means button is pressed because of INPUT_PULLUP
  // digitalRead tells us the signal (0 -> LOW, 1-> HIGH) given off from the button when pressed
  // We store it in a boolean type variable if digitalRead finds buttonPin to be LOW it will equate to TRUE which is stored in the dispenseCandy variable

  // if user wants to dispenseCandy (dispenseCandy == True) we turn on the LED (HIGH) and rotate the wheel 1 full cycle (360 from original position)

  if (dispenseCandy) {
    digitalWrite(ledPin, HIGH); // LED ON fvf

    // 1 full motor step = 1.8 degrees
    // We need 360 degrees -> 1.8 * x = 360 -> 360/1.8 = 200 steps
    // We need to make it go that amount of steps
    for (int i=0; i < 200; i++) { // this is 200 steps
      // 1 Step -> (Beginning)
      digitalWrite(stePin, HIGH); // Starts the step pulse (motor takes a step/moves certain amount) pin goes to 5V
      delayMicroseconds(7000); // 5000 microseconds makes it run smoothly // lower this number the faster it goes
      digitalWrite(stePin, LOW); // pin goes to 0 volts
      delayMicroseconds(7000);
      // 1 Step -> (Ending)
    }

    digitalWrite(ledPin, LOW); // So the light waits till after the 360 degree turn

  }

}

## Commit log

2026-06-29 Create CAD folder
2026-06-29 Create schematics folder
2026-06-29 Create 3D printing stl files folder
2026-06-29 Create wiring diagrams folder
2026-06-30 Create assembly images folder
2026-06-30 Add entry for 12" Clear Acrylic Tube in README
